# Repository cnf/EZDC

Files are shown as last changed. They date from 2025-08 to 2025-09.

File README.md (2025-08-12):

# EZCPAP

EZCPAP is a BLDC driver for [CPAP blower motors](https://www.ifixit.com/Guide/ResMed+AirSense+10+Pump+Motor+Replacement/137050) that fits in a BTT EZDriver socket, such as on an [SKR EZ](https://bttwiki.com/SKR%203%20EZ.html).

It effectively acts like a motor driver on a 3d printer. which you can then use to drive a CPAP motor for part cooling.

!! Still in the conceptual/development phase !!

[View in kicanvas](https://kicanvas.org/?github=https%3A%2F%2Fgithub.com%2Fcnf%2FEZCPAP)

## Concept render
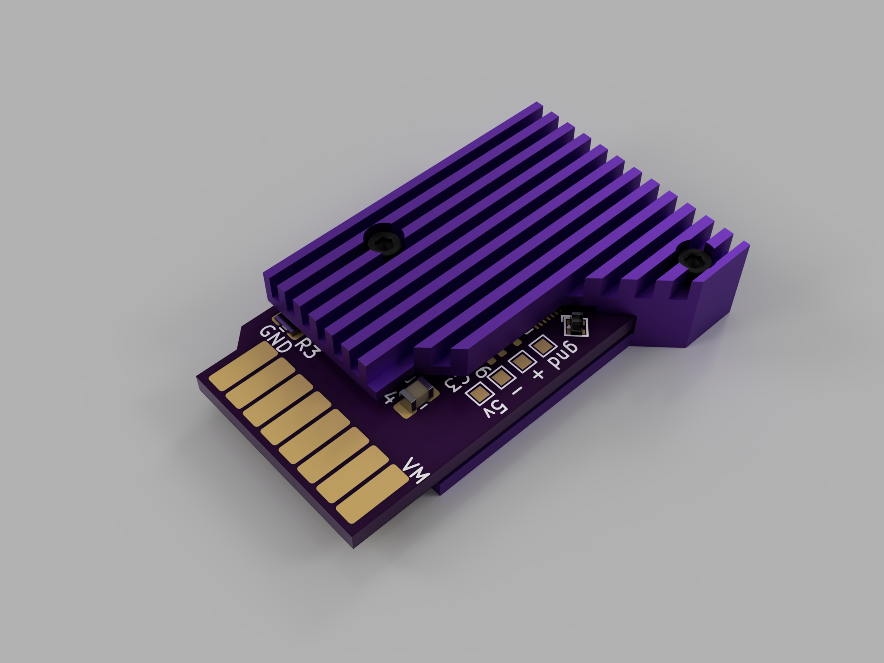
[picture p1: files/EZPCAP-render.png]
EZPCAP with heatsink

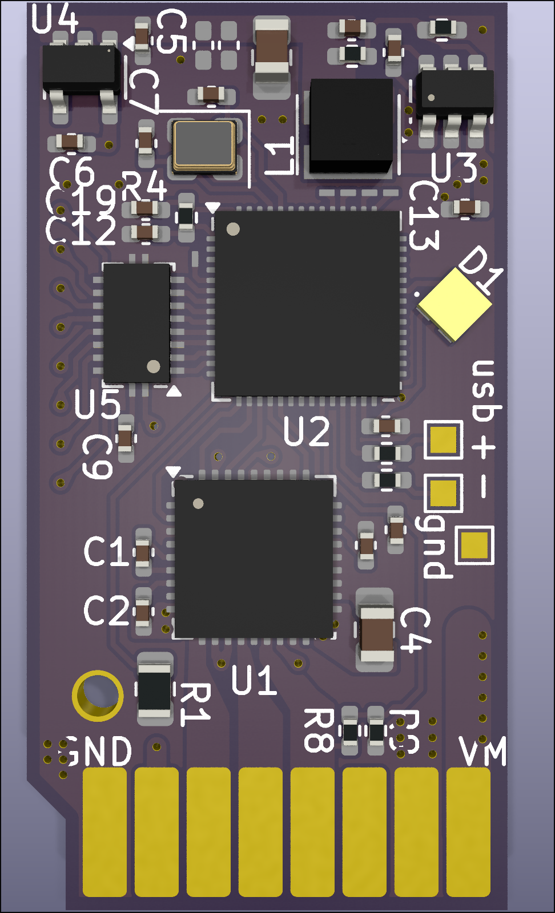
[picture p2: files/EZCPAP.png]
EZCPAP


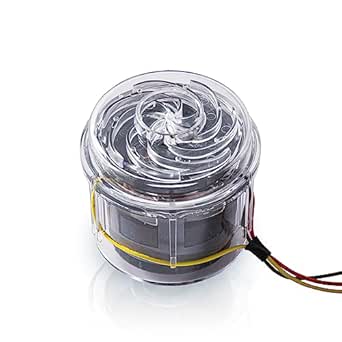
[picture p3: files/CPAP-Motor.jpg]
CPAP Motor


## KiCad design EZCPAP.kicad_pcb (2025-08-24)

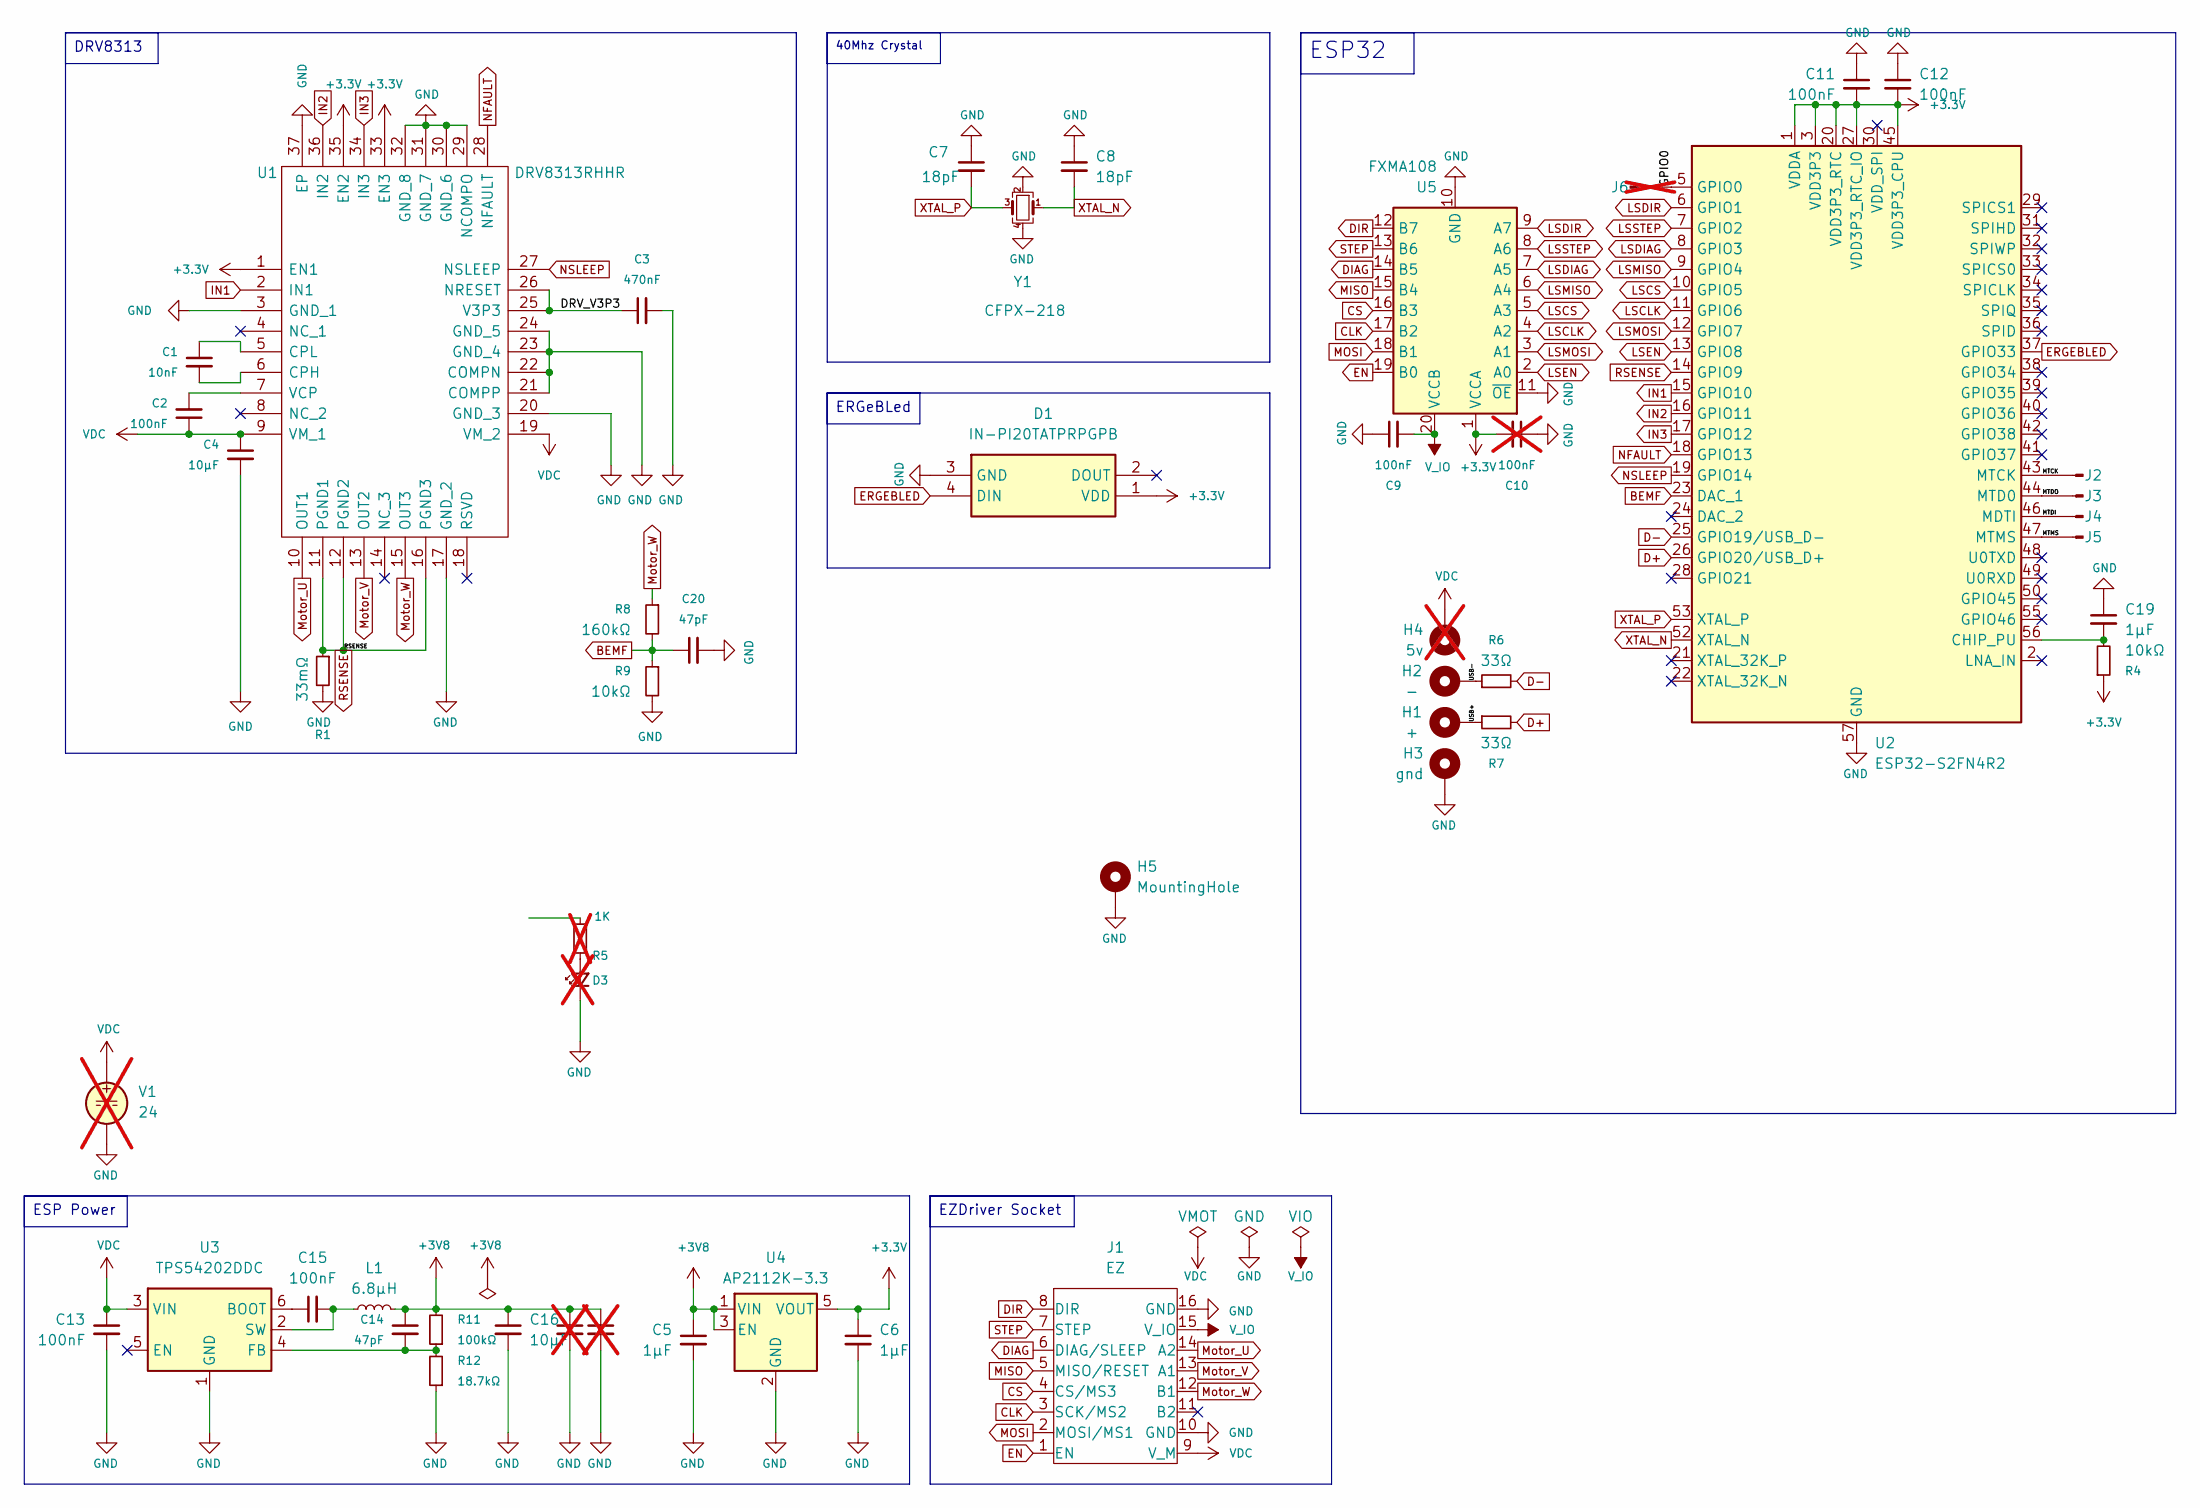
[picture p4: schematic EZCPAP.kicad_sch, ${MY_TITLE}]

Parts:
C1: 10nF; C_0402_1005Metric_Pad0.74x0.62mm_HandSolder
C2, C9, C11, C12, C13, C15: 100nF; C_0402_1005Metric_Pad0.74x0.62mm_HandSolder
C3: 470nF; C_0402_1005Metric_Pad0.74x0.62mm_HandSolder
C4, C16: 10µF; C_0805_2012Metric_Pad1.18x1.45mm_HandSolder
C5, C6, C19: 1µF; C_0402_1005Metric_Pad0.74x0.62mm_HandSolder
C7, C8: 18pF; C_0402_1005Metric_Pad0.74x0.62mm_HandSolder
C10: 100nF; C_0402_1005Metric_Pad0.74x0.62mm_HandSolder; LCSC Part C307331; not fitted
C14, C20: 47pF; C_0402_1005Metric_Pad0.74x0.62mm_HandSolder
C17, C18: NaN; C_0402_1005Metric_Pad0.74x0.62mm_HandSolder; LCSC Part C23733; not fitted
D1: IN-PI20TATPRPGPB; LED_2020; Manufacturer_Part_Number IN-PI20TATPRPGPB; Mouser Part Number 743-IN-PI20TATPRPGPB
D3: Green; LED_0402_1005Metric; not fitted
H1: +; TestPoint_Pad_1.0x1.0mm
H2: -; TestPoint_Pad_1.0x1.0mm
H3: gnd; TestPoint_Pad_1.0x1.0mm
H4: 5v; TestPoint_Pad_1.0x1.0mm; not fitted
H5: MountingHole; Hole
J1: EZ; EZDriver
J2, J3, J4, J5: Conn_01x01_Pin; Pin Exposed Pad
J6: Conn_01x01_Pin; Pin Exposed Pad; not fitted
L1: 6.8µH; L_Wurth_WE-MAPI-3020; Part Number 74438336068HT
R1: 33mΩ; R_0805_2012Metric
R4, R9: 10kΩ; R_0402_1005Metric_Pad0.72x0.64mm_HandSolder
R5: 1K; R_0402_1005Metric_Pad0.72x0.64mm_HandSolder; not fitted
R6, R7: 33Ω; R_0402_1005Metric_Pad0.72x0.64mm_HandSolder
R8: 160kΩ; R_0402_1005Metric_Pad0.72x0.64mm_HandSolder
R11: 100kΩ; R_0402_1005Metric_Pad0.72x0.64mm_HandSolder
R12: 18.7kΩ; R_0402_1005Metric_Pad0.72x0.64mm_HandSolder
U1: DRV8313RHHR; DRV8313RHH; Manufacturer PN DRV8313RHHR; LCSC Part C165154
U2: ESP32-S2FN4R2; QFN-56-1EP_7x7mm_P0.4mm_EP4x4mm_ThermalVias; LCSC Part C2844252
U3: TPS54202DDC; SOT-23-6; LCSC Part C191884
U4: AP2112K-3.3; SOT-23-5; LCSC Part C51118
U5: FXMA108; WQFN-20-1EP_2.5x4.5mm_P0.5mm_EP1x2.9mm; LCSC Part C891320
V1: 24; not fitted
Y1: CFPX-218; Crystal_SMD_2520-4Pin_2.5x2.0mm; Manufacturer PN 830108208709

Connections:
+3.3V: C6.1, C10.2, C11.2, C12.2, D1.1 (VDD), R4.1, U1.1 (EN1), U1.33 (EN3), U1.35 (EN2), U2.1 (VDDA), U2.3 (VDD3P3), U2.4 (VDD3P3), U2.20 (VDD3P3_RTC), U2.27 (VDD3P3_RTC_IO), U2.45 (VDD3P3_CPU), U2.51 (VDDA), U2.54 (VDDA), U4.5 (VOUT), U5.1 (VCCA)
+3V8: C5.1, C14.1, C16.1, C17.1, C18.1, L1.2, R11.2, U4.1 (VIN), U4.3 (EN)
/DRV_V3P3: C3.1, U1.25 (V3P3), U1.26 (NRESET)
/GPIO0: J6.1, U2.5 (GPIO0)
/MTCK: J2.1, U2.43 (MTCK)
/MTDI: J4.1, U2.46 (MDTI)
/MTDO: J3.1, U2.44 (MTD0)
/MTMS: J5.1, U2.47 (MTMS)
/USB+: H1.1, R7.1
/USB-: H2.1, R6.1
BEMF: C20.1, R8.2, R9.1, U2.23 (DAC_1)
CLK: J1.3 (SCK/MS2), U5.17 (B2)
CS: J1.4 (CS/MS3), U5.16 (B3)
D+: R7.2, U2.26 (GPIO20/USB_D+)
D-: R6.2, U2.25 (GPIO19/USB_D-)
DIAG: J1.6 (DIAG/SLEEP), U5.14 (B5)
DIR: J1.8 (DIR), U5.12 (B7)
EN: J1.1 (EN), U5.19 (B0)
ERGEBLED: D1.4 (DIN), U2.37 (GPIO33)
GND: C3.2, C4.2, C5.2, C6.2, C7.1, C8.1, C9.1, C10.1, C11.1, C12.1, C13.2, C16.2, C17.2, C18.2, C19.1, C20.2, D1.3 (GND), D3.1 (K), H3.1, H5.1, J1.10 (GND), J1.16 (GND), R1.2, R9.2, R12.1, U1.3 (GND_1), U1.17 (GND_2), U1.20 (GND_3), U1.21 (COMPP), U1.22 (COMPN), U1.23 (GND_4), U1.24 (GND_5), U1.29 (NCOMPO), U1.30 (GND_6), U1.31 (GND_7), U1.32 (GND_8), U1.37 (EP), U2.57 (GND), U3.1 (GND), U4.2 (GND), U5.10 (GND), U5.11 (~OE), V1.2, Y1.2, Y1.4
IN1: U1.2 (IN1), U2.15 (GPIO10)
IN2: U1.36 (IN2), U2.16 (GPIO11)
IN3: U1.34 (IN3), U2.17 (GPIO12)
LSCLK: U2.11 (GPIO6), U5.4 (A2)
LSCS: U2.10 (GPIO5), U5.5 (A3)
LSDIAG: U2.8 (GPIO3), U5.7 (A5)
LSDIR: U2.6 (GPIO1), U5.9 (A7)
LSEN: U2.13 (GPIO8), U5.2 (A0)
LSMISO: U2.9 (GPIO4), U5.6 (A4)
LSMOSI: U2.12 (GPIO7), U5.3 (A1)
LSSTEP: U2.7 (GPIO2), U5.8 (A6)
MISO: J1.5 (MISO/RESET), U5.15 (B4)
MOSI: J1.2 (MOSI/MS1), U5.18 (B1)
Motor_U: J1.14 (A2), U1.10 (OUT1)
Motor_V: J1.13 (A1), U1.13 (OUT2)
Motor_W: J1.12 (B1), R8.1, U1.15 (OUT3)
NFAULT: U1.28 (NFAULT), U2.18 (GPIO13)
NSLEEP: U1.27 (NSLEEP), U2.19 (GPIO14)
unnamed: D3.2 (A), R5.1
unnamed: C1.2, U1.6 (CPH)
unnamed: C1.1, U1.5 (CPL)
unnamed: C2.2, U1.7 (VCP)
unnamed: C19.2, R4.2, U2.56 (CHIP_PU)
unnamed: C15.1, U3.6 (BOOT)
unnamed: C14.2, R11.1, R12.2, U3.4 (FB)
unnamed: C15.2, L1.1, U3.2 (SW)
RSENSE: R1.1, U1.11 (PGND1), U1.12 (PGND2), U1.16 (PGND3), U2.14 (GPIO9)
STEP: J1.7 (STEP), U5.13 (B6)
VDC: C2.1, C4.1, C13.1, H4.1, J1.9 (V_M), U1.9 (VM_1), U1.19 (VM_2), U3.3 (VIN), V1.1
V_IO: C9.2, J1.15 (V_IO), U5.20 (VCCB)
XTAL_N: C8.2, U2.52 (XTAL_N), Y1.1
XTAL_P: C7.2, U2.53 (XTAL_P), Y1.3

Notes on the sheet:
40Mhz Crystal
DRV8313
ERGeBLed
ESP32
EZDriver Socket
ESP Power

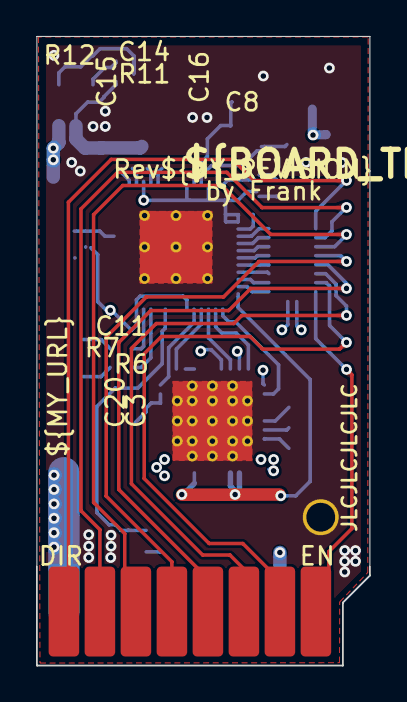
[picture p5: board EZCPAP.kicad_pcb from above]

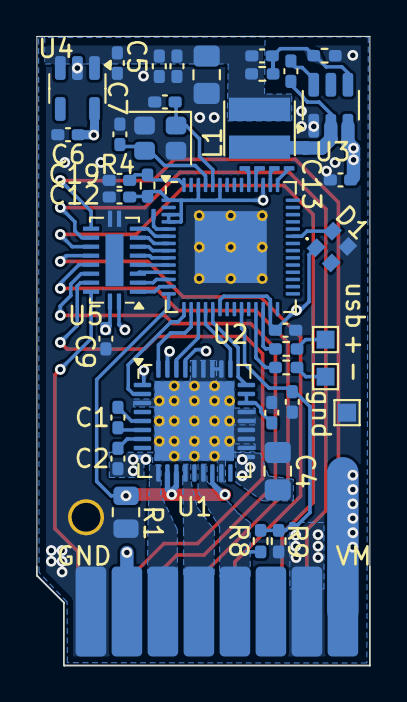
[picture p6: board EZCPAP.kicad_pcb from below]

Board: 4 copper layers, 18.5 x 35.0 mm, 45 parts (44 on the bottom side), 51 nets.

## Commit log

2025-08-10 right level shifter ref networks, and small changes
    [EZCPAP.kicad_pcb, EZCPAP.kicad_sch]
2025-08-10 Adding extra footprints/symbols to project
    [EZCPAP.kicad_sch]
2025-08-10 moar cleanup n stuff
    [EZCPAP.kicad_pcb, EZCPAP.kicad_sch]
2025-08-10 moved via intercecting with a trace
    [EZCPAP.kicad_pcb]
2025-08-12 added hole, etc
    [EZCPAP.kicad_pcb, EZCPAP.kicad_sch]
2025-08-12 more cleanup, hard enable, but link nsleep
    [EZCPAP.kicad_pcb, EZCPAP.kicad_sch]
2025-08-18 maybe final
    [EZCPAP.kicad_pcb, EZCPAP.kicad_sch]
2025-08-18 full vias, and small edits
    [EZCPAP.kicad_pcb]
2025-08-21 maybe, maybe final?
    [EZCPAP.kicad_pcb, EZCPAP.kicad_sch]
2025-08-22 final, finaller, est?
    [EZCPAP.kicad_pcb, EZCPAP.kicad_sch]
2025-08-24 final, finaller, ist?
    [EZCPAP.kicad_pcb, EZCPAP.kicad_sch]
2025-09-22 Update PCB Rendering
2025-10-08 Rev B, initial
    [EZCPAP.kicad_sch]
2025-10-09 Rev B, RC2
    [EZCPAP.kicad_sch]
2025-10-24 adding test points
    [EZCPAP.kicad_sch]
